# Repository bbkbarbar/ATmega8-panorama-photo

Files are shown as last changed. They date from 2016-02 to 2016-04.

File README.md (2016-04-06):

# Panorama-photo

## Project goal:
Create a device what can rotate camera (or camera-mounted phone) around Z axis to create perfect panorama photos or time-lapse videos.

### Functionality:
With this device the **user can create panorama photos** without "fitting problems"  
**or** can create **time-lapse videos with** using (very) slowly **rotating camera**.  
This device can be placed between any standard camera-tripod (or any other camera-mount) and the camera (or any other device what can be placed on a standard tripod (will be called as "camera" below)).
It can rotate the camera to selected direction with selected speed.
The device works from standard lithium battery with built-in battery charger.

### Features:
 - User can select the direction of rotating
 - User can select the speed of rotating
 - Device can be mounted in any standard tripod (or any other device what uses standard mount-screw)
 - Any camera, cellphone mount or any other devices can be mounted on the top of this device which can be mounted on a standard tripod
 - User can set the position of mounted device in 2 axis to reach the optimal position of camera (where the camera's lens is exactly above the center point of rotation)
 - Works with using a replaceable Li-ion battery (in size of 18650)
 - Contains built-in battery charger module (charging current max 1A from micro-usb port)
 - User can interrupt the process during rotation. (since v1.2) 

### MCU: 
**Required features:**
 - PWM output (~50Hz) (1)
 - Analog input (at least 2 channel)
 - I/O input (at least 2)
 - I/O output (at least 2)
 - Low energy consumption
 
**Selected device** (MCU): Atmel **AVR ATmega8** ([DataSheet](https://github.com/bbkbarbar/ATmega8-panorama-photo/blob/master/Docs/ATmega8_datasheet.pdf))

#### Sequence diagram of states (v1.2)
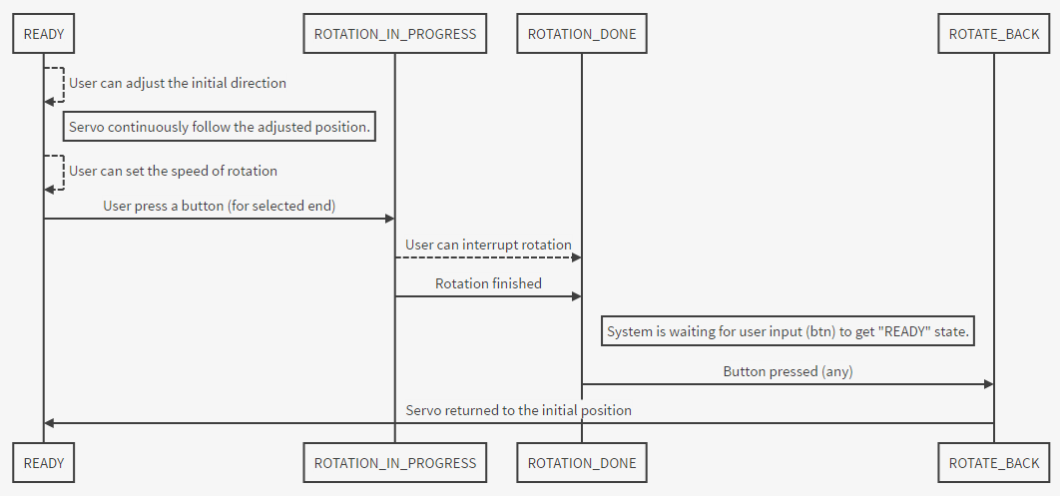
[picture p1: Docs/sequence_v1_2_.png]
Basic sequence diagram


#### First "mainly working" version on testboard:

<a href="http://www.youtube.com/watch?i8isvKmdPvMfeature=player_embedded&v=33iNxKAsr9w
" target="_blank">IMAGE ALT TEXT HERE</a>

#### First test device (mechanism and box built from Lego):
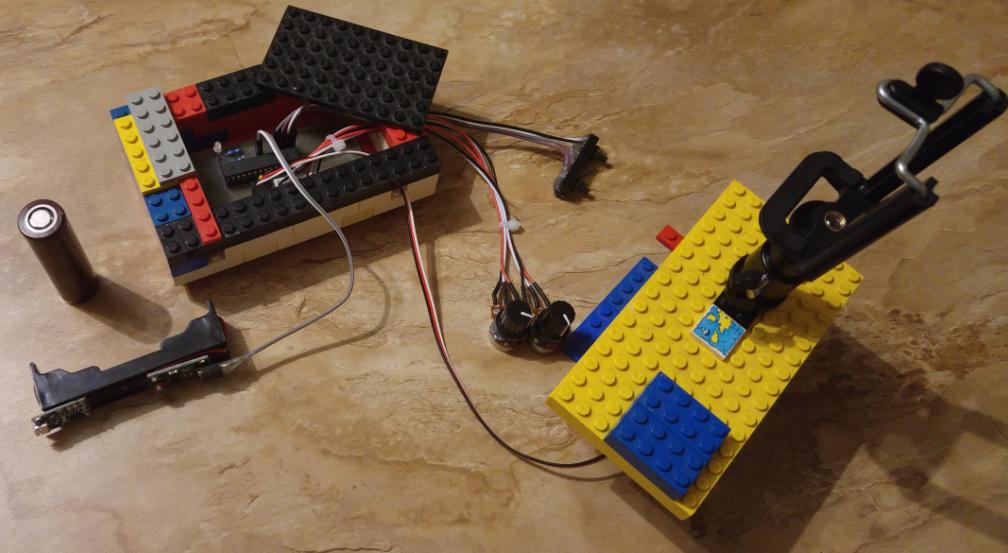
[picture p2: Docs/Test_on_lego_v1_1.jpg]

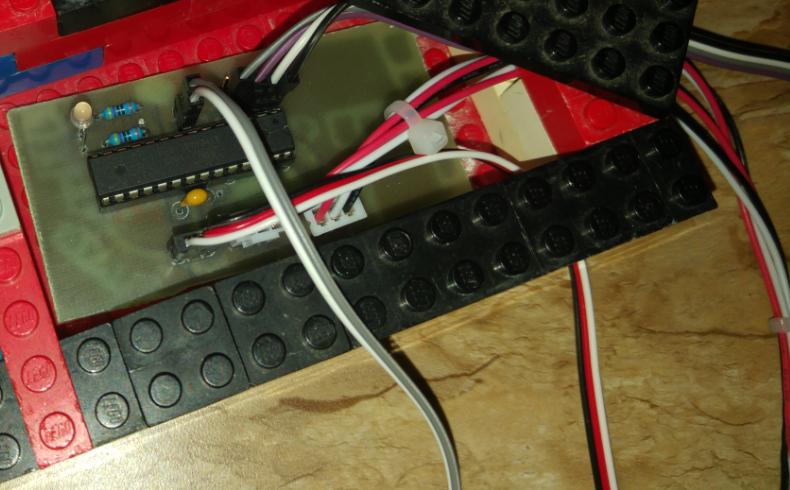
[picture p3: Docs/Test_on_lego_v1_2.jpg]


**[Photo album](https://goo.gl/photos/7FJK6yykkkFa5fTw9)**

**UseCase diagram**

[First version can be seen here..](https://github.com/bbkbarbar/ATmega8-panorama-photo/blob/master/Docs/useCase_plan_1.png)

[Previous test #1](https://youtu.be/i8isvKmdPvM)

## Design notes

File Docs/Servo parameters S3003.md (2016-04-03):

# Servo type: Futaba S3003
https://www.servocity.com/html/s3003_servo_standard.html#.VwD2R5yLSt9

Control System:                 +Pulse Width Control 1520usec Neutral
Required Pulse:                 3-5 Volt Peak to Peak Square Wave
Operating Voltage:              4.8-6.0 Volts
Operating Temperature Range: 	-20 to +60 Degree C
Operating Speed (4.8V):         0.23sec/60 degrees at no load
Operating Speed (6.0V):         0.19sec/60 degrees at no load
Stall Torque (4.8V):            44 oz/in. (3.2kg.cm)
Stall Torque (6.0V):            56.8 oz/in. (4.1kg.cm)
Operating Angle:                45 Deg. one side pulse traveling 400usec
Continuous Rotation Modifiable: Yes
Direction:                      Counter Clockwise/Pulse Traveling 1520-1900usec
Current Drain (4.8V):           7.2mA/idle
Current Drain (6.0V):           8mA/idle
Motor Type:                     3 Pole Ferrite
Potentiometer Drive:            Indirect Drive 
Bearing Type:                   Plastic Bearing
Gear Type:                      All Nylon Gears
Connector Wire Length:          12" (~305mm)
Dimensions:                     1.6" x 0.8"x 1.4" (41 x 20 x 36mm)
Weight:                         1.3oz. (37.2g)

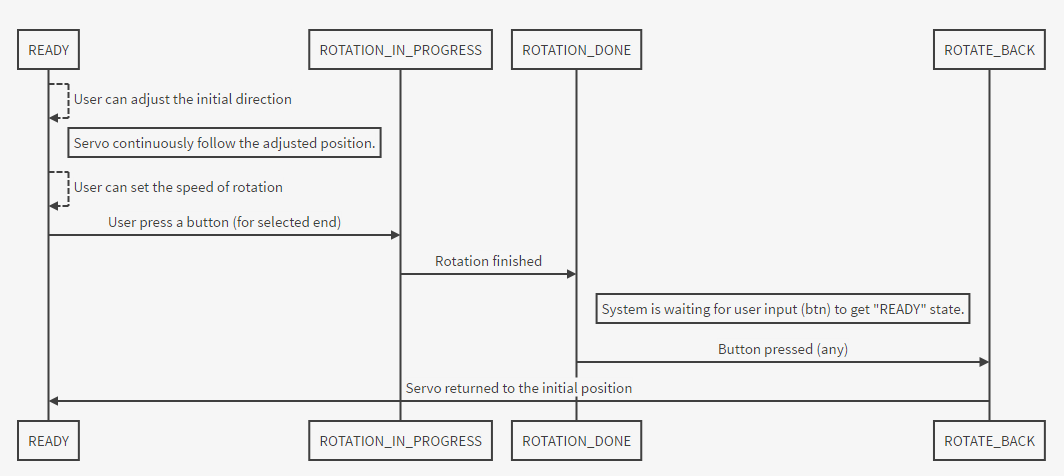
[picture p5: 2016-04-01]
Docs/sequence_v1_1_.png

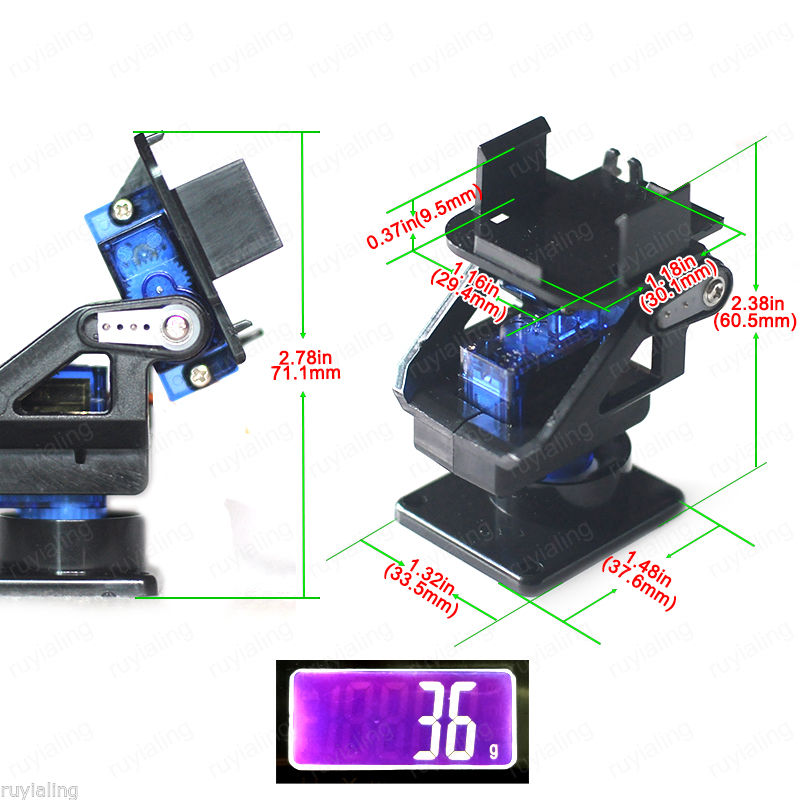
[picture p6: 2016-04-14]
Docs/Servo_hw/Servo_arm_for_phones.jpg

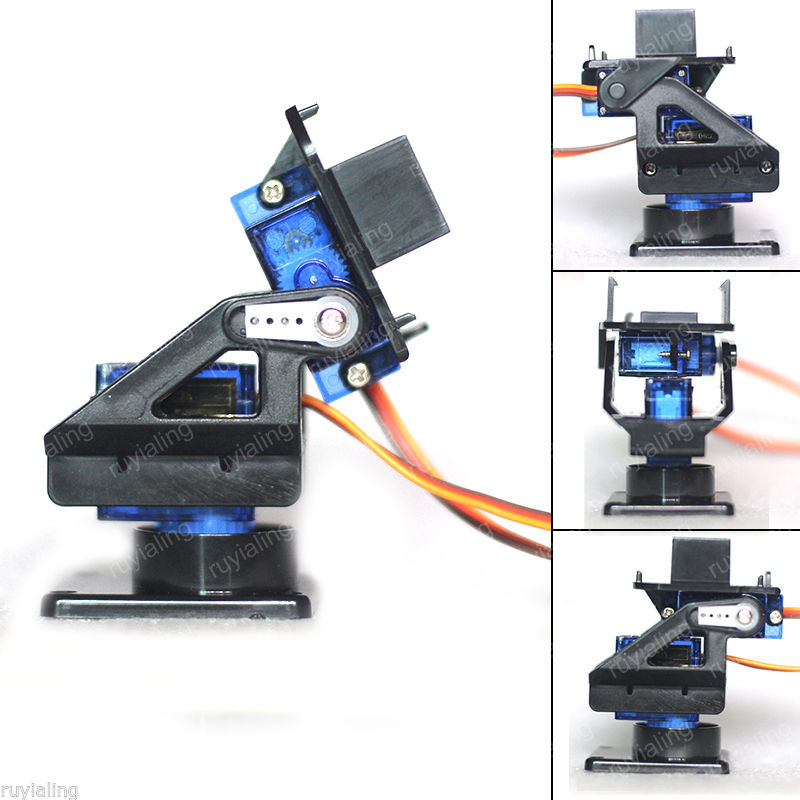
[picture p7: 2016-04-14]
Docs/Servo_hw/Servo_arm_for_phones (1).jpg

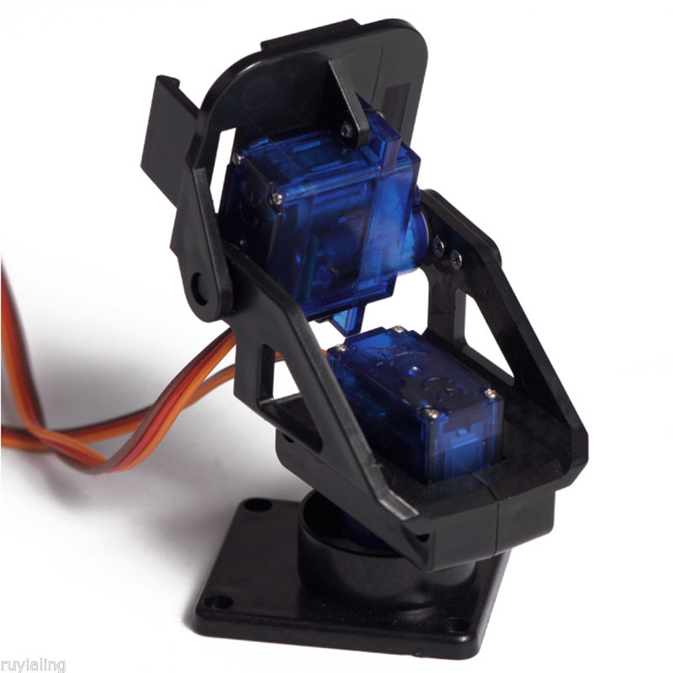
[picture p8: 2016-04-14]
Docs/Servo_hw/Servo_arm_for_phones (2).jpg

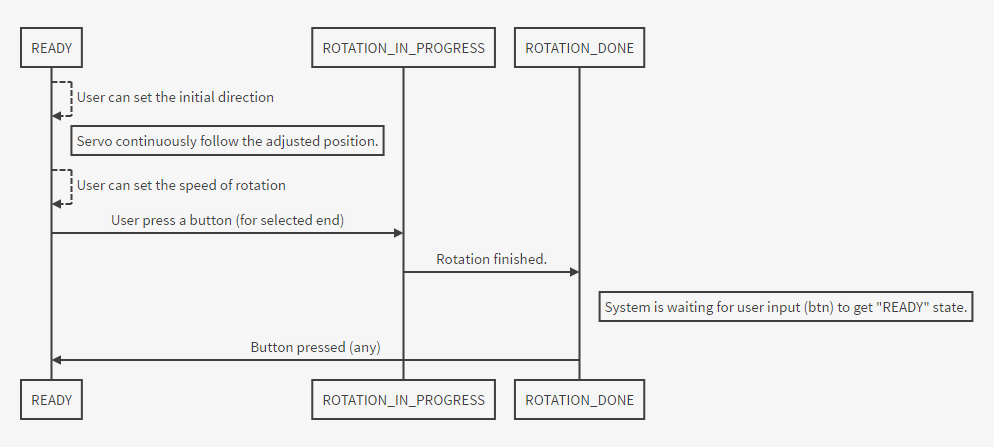
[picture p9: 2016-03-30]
Docs/Sequence.png

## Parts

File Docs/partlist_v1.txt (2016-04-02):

Partlist

Exported from ATmega8_panorama-photo_v2.sch at 2016.04.02. 10:25:53

EAGLE Version 5.10.0 Copyright (c) 1988-2010 CadSoft

Part            	Device							Package  	Library  		

ATMEGA8             DIL28-3      					DIL28-3    	ic-package
C1                  Ceramic capacitator     		C2.5-3     	capacitor-wima
LED_RG              connector - 3 pin				MA03-1     	con-lstb
POT1                connector - 3 pin				MA03-1     	con-lstb
POT2            	connector - 3 pin				MA03-1     	con-lstb
PWR_SUPPLY_CONN     connector - 2 pin				22-23-2021 	con-molex
R1                  R-EU_0204/7  					0204/7     	resistor
R2                  R-EU_0204/7  					0204/7     	resistor
R5                  R-EU_0207/5V 					0207/5V    	resistor
R6                  R-EU_0207/5V 					0207/5V    	resistor
SERVO               connector - 3 pin				MA03-1     	con-lstb
SV1                 connector - 2x3 pin or 1x4 pin	MA03-2     	con-lstb

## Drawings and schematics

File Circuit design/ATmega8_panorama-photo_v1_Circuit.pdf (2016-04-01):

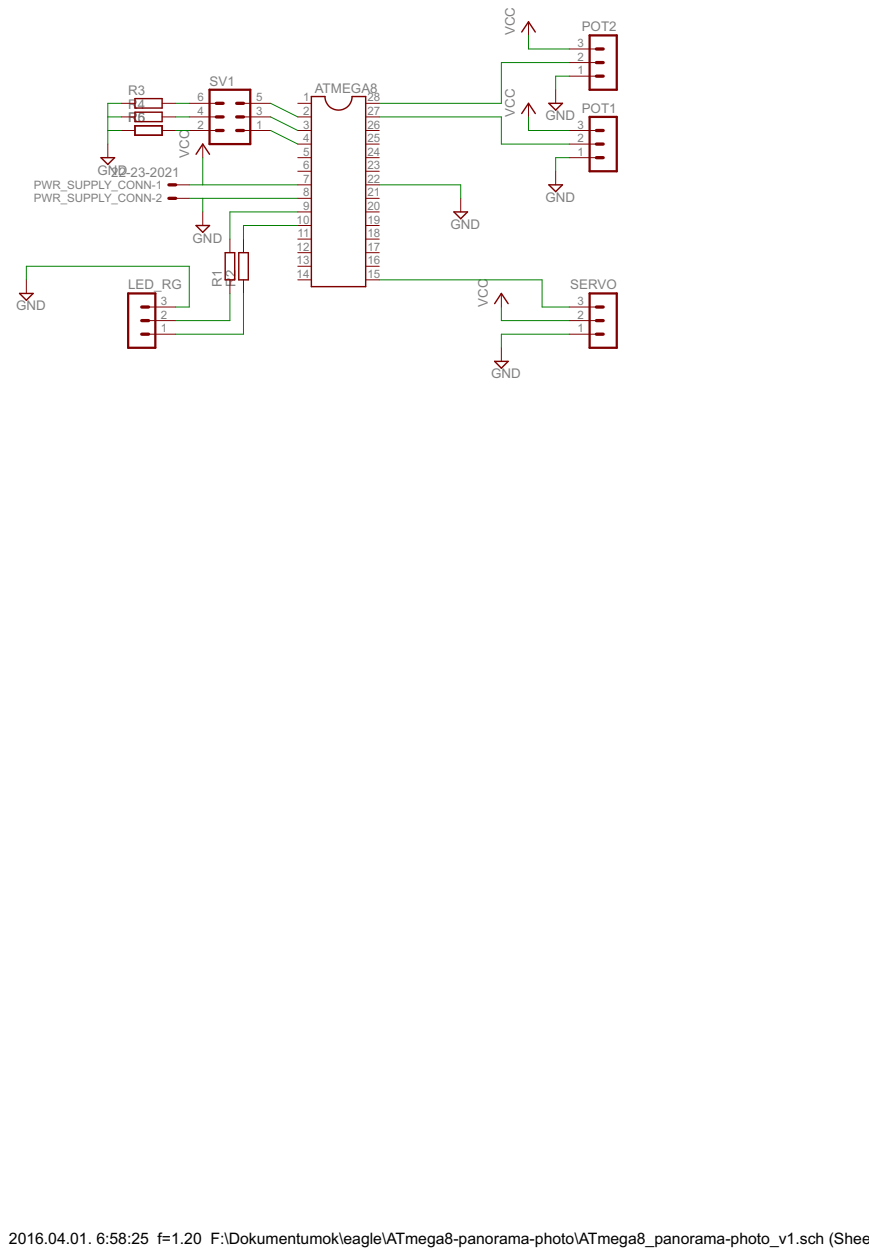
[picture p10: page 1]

2016.04.01. 6:58:25 f=1.20 F:\Dokumentumok\eagle\ATmega8-panorama-photo\ATmega8_panorama-photo_v1.sch (Sheet: 1/1)

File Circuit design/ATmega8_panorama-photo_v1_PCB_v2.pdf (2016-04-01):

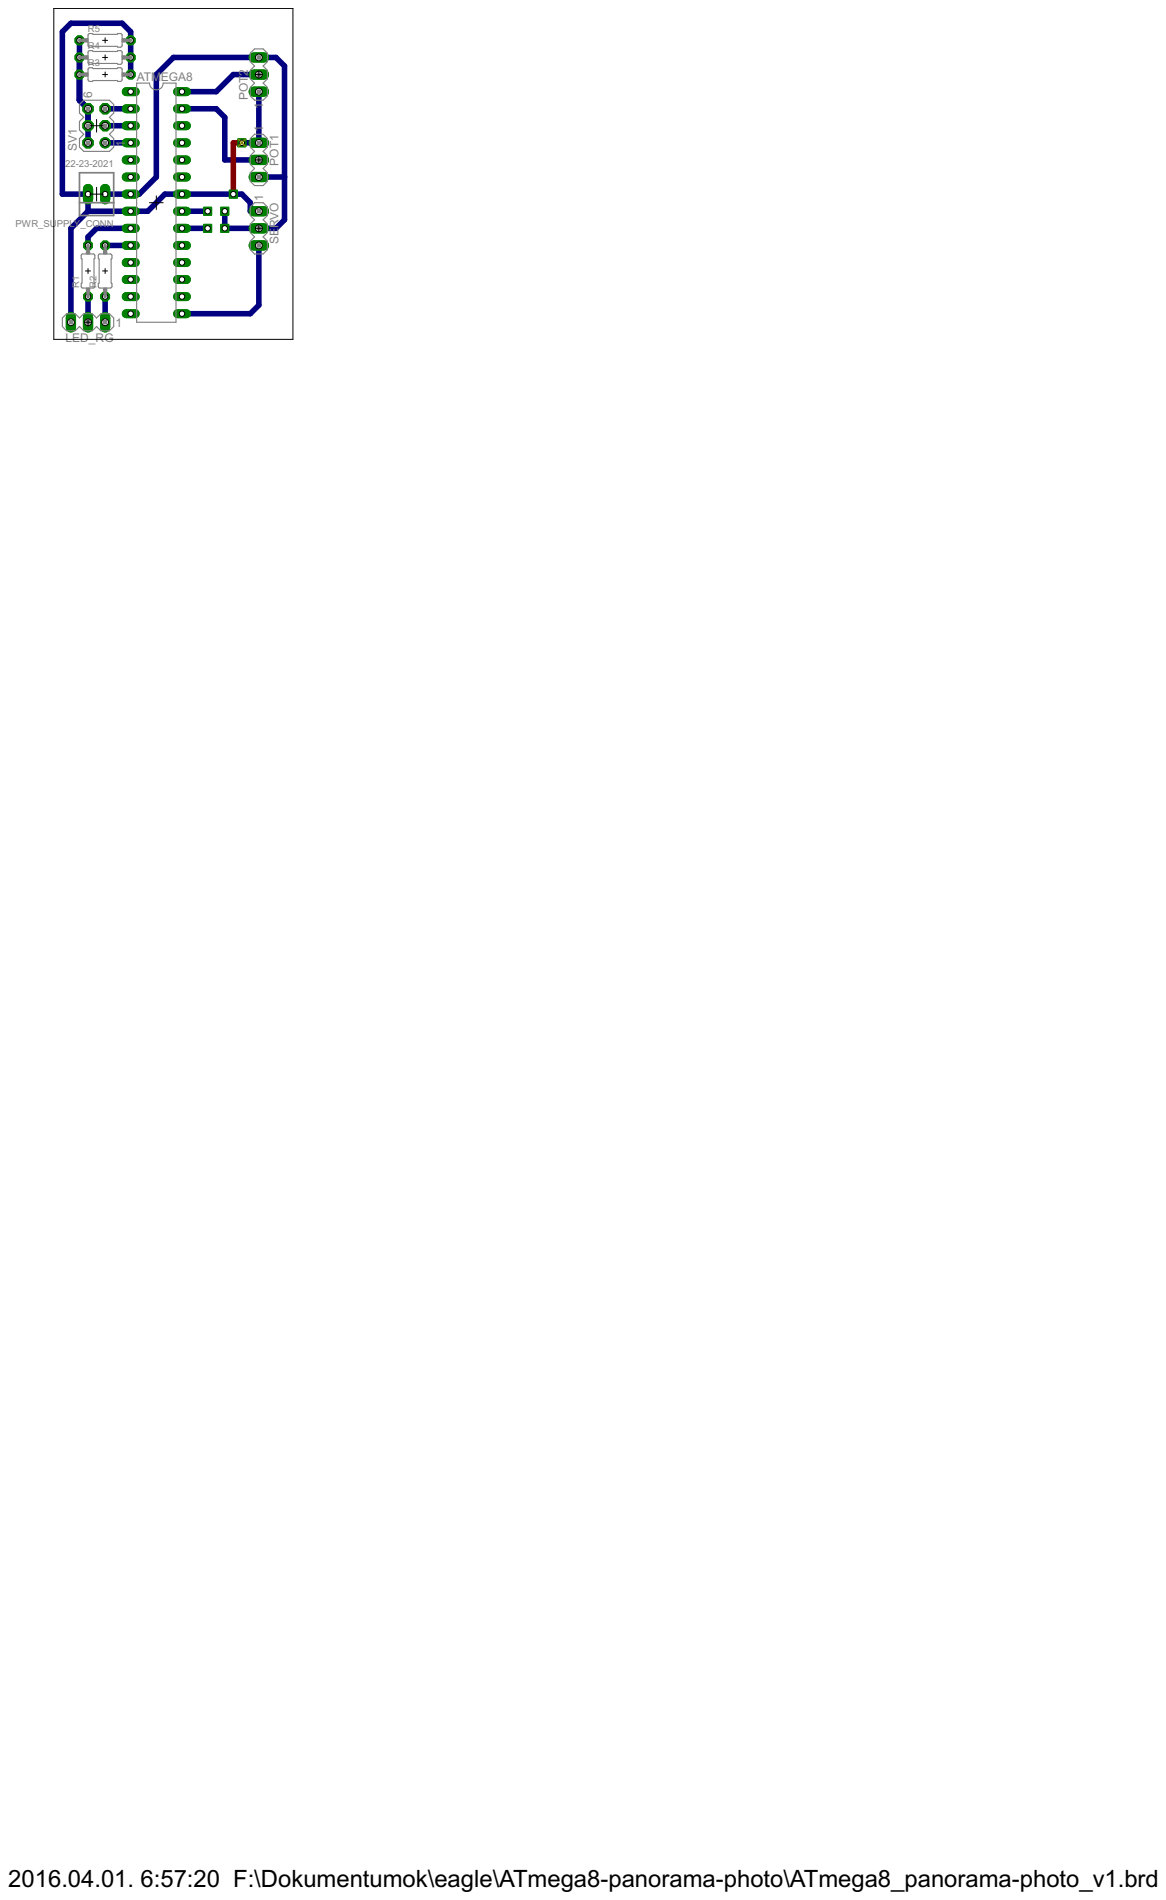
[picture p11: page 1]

2016.04.01. 6:57:20 F:\Dokumentumok\eagle\ATmega8-panorama-photo\ATmega8_panorama-photo_v1.brd

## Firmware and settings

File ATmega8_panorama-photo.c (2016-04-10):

 /*************************************\
 *        Panorama-photo v1.2          *
 *                                     *
 *  Device: ATmega8                    *
 *          mega8L-8PU - OK            *
 *          mega8-16PU - ??            *
 *  Deploy configuration:              *
 *   SUT_CKSEL: ________               *
 *   ISP freq: 115.2 kHz               *
 *                                     *
 *                                     *
 *  Pin configuration:                 *
 *   @used:                            *
 *   - Button 1:   PD0                 *
 *   - Button 2:   PD1                 *
 *   - Potmeter 1: PC5 (ch5)           *
 *   - Potmeter 2: PC4 (ch4)           *
 *   - Servo:      PB1 (OC1A)          *
 *   - LED1-green: PB7                 *
 *   - LED1-red:   PB6                 *
 *                                     *
 *  Pin configuration @TEST:           *
 *   - Button 1:   PB5                 *
 *   - Button 2:   PB4                 *
 *   - LEDBAR:     PD0-7               *
 *                                     *
 *  Test: WORKS on target board v1.0   *
 *                                     *
 *         Boor Andras  @ 2016         *
 *                                     *
 \*************************************/

//#define TEST
//#define SPIKE
#define TESTBOARD
//#define ENABLE_ROTATE_BACK

#define F_CPU 1000000

#include "lib/ATmega8_read_ADC.c"
#include "lib/ATmega8_servo_control.c"
#ifdef TESTBOARD
#include "lib/bar_display.c"
#endif


#ifndef DELAY_INCLUDED
    #include <util/delay.h>
    #define DELAY_INCLUDED
#endif


/////////////////////////////////////     HW DEFINITIONS    /////////////////////////////////////
// LED
#define PORT_OF_LEDS                PORTB
#define LED_PIN_GREEN               7
#define LED_PIN_RED                 6

// BUTTON
#ifndef TESTBOARD
    #define PORT_INPUT_OF_BUTTONS   PIND
    #define PORT_OF_BUTTONS         PORTD
    #define BUTTON_1_PIN            0
    #define BUTTON_2_PIN            1
#else
    #define PORT_INPUT_OF_BUTTONS   PINB
    #define PORT_OF_BUTTONS         PORTB
    #define BUTTON_1_PIN            5
    #define BUTTON_2_PIN            4
#endif
//#define BUTTON_3_PIN              2                                         // inactive in v1

#define BTN_1                       (PORT_INPUT_OF_BUTTONS >> BUTTON_1_PIN)
#define BTN_2                       (PORT_INPUT_OF_BUTTONS >> BUTTON_2_PIN)
//#define PIN_BTN_3                 (PORT_INPUT_OF_BUTTONS >> BUTTON_3_PIN)   // inactive in v1
#define BTN_RIGHT                   BTN_1
#define BTN_LEFT                    BTN_2

// Read button states
#define isPressed(x)                ((x & 0b1) == 0)
#define isReleased(x)               ((x & 0b1) == 1)


// ADC channels of potmeters
#define POT_TEST                    0
#define POT1                        5
#define POT2                        4

// States of feedback LED
#define OFF                         0
#define GREEN                       1
#define RED                         2
#define YELLOW                      3

#ifdef TESTBOARD
    #define LEDBAR                  PORTD
#endif

//////////////////////////////////////        OTHERS         ////////////////////////////////////
#define DEFAULT_DELAY               100

#define POT_MAX_VALUE               1023

#define RIGHT_END_POSITION          SERVO_RIGHT
#define LEFT_END_POSITION           SERVO_LEFT

// Identify direction (of previously pressed button)
#define NONE                        0
#define RIGHT                       1
#define LEFT                        2

#define INC_TO_RIGHT                (-1)
#define INC_TO_LEFT                 (1)


// System wait for BUTTON_RELEASE_DELAY ms before do the next command
// to avoid unwanted re-detection of buttonPress on same button.
#define BUTTON_RELEASE_DELAY        500

// Minimum delay in continous rotation to prevent from to fast rotating
#define MIN_DELAY_FOR_ROTATION      50

// TRY to prevent servo "quake" symptom
#define DELAY_AFTER_SERVO_ROTATION_IN_READY_STATUS 30

// For using tighten servo degree to prevent problems 
// coused by servo's internal limit-detection
#define SERVO_EDGE_THRESHOLD        100

// Used when system is in "ROTATE_BACK" state
// and need to determine when servo almost reached the adjusted initial position
#define SERVO_ROTATE_BACK_THRESHOLD 50

//////////////////////////////////////        STATES         ////////////////////////////////////
// Ready to use. User can set initial direction and speed.
// System is waiting for start input (btn). (Servo continuously follow the setted position.)
#define READY                       1
// Rotation started, but not finished yet.
#define ROTATION_IN_PROGRESS        2
// Rotation finished.System is waiting for user input (btn) to get "ROTATE_BACK" state.
#define ROTATION_DONE               3
// Servo rotating back before get "READY" state.
#define ROTATE_BACK                 4


// Additional information can be displayed on ledbar (in unused io-ports)
// when configuration runs in testboard.
#ifdef TESTBOARD
    void showValueOnLedBar(unsigned short value, unsigned short min, unsigned short max){
        LEDBAR = getValueToShow(
            value - min, 
            max - min
        );
    }
#endif


// Wait function can be used instead of direct usage of "_delay_ms(val)" function
// because of the input range problem of "_dalay_ms()" function.
void wait(unsigned short val) {
    while(val--) _delay_ms(1);
}

void _wait(){
    _delay_ms(DEFAULT_DELAY);
}


// Set color of feedback led (RG)
void setLed(unsigned short color){
    if(color == GREEN){
        PORT_OF_LEDS &= ~(1 << LED_PIN_RED); 
        PORT_OF_LEDS |=  (1 << LED_PIN_GREEN);
    }else
    if(color == RED){
        PORT_OF_LEDS |=  (1 << LED_PIN_RED); 
        PORT_OF_LEDS &= ~(1 << LED_PIN_GREEN);
    }else
    if(color == YELLOW){
        PORT_OF_LEDS |=  (1 << LED_PIN_RED); 
        PORT_OF_LEDS |=  (1 << LED_PIN_GREEN);
    }else{
        PORT_OF_LEDS &= ~(1 << LED_PIN_RED); 
        PORT_OF_LEDS &= ~(1 << LED_PIN_GREEN);
    }
}


// Determine conditions when servo reached any end position
#define isRotationDone() ( ((btnPressedPreviously == RIGHT && (getServoPosition() > RIGHT_END_POSITION + SERVO_EDGE_THRESHOLD)) || (btnPressedPreviously == LEFT && (getServoPosition() < LEFT_END_POSITION - SERVO_EDGE_THRESHOLD)))?0:1 )


// Calculate difference between given values (can not be negative)
unsigned short diff(unsigned short x, unsigned short y){
    return ( ((x)>(y))?((x)-(y)):((y)-(x)) );
}


// Modify servo direction with given value
void rotateServo(short value){
    setServoPosition( getServoPosition() + value );
}


// Calculate delay between iteration steps of rotation
unsigned short calculateDelayOfRotationSteps(uint16_t speedInput){
    return (unsigned short)( MIN_DELAY_FOR_ROTATION + speedInput );
}


// Calculate servoPosition from potmeter input
unsigned short calculateServoPositionFromDirectionInput(uint16_t positionInput){
    return ( ((unsigned short) (POT_MAX_VALUE - positionInput) * 1.9f) + SERVO_OUTPUT_MIN );
}


void init(){   
    //                 LED
    // Set LED pins as output
    DDRB |= (1 << LED_PIN_GREEN) 
         |  (1 << LED_PIN_RED);

    //              POTMETERS
    // DDRC set as input for ADC in initADC() function

    //                SERVO
    // Output of servo set as output initServoControl() function
          
    //DDRB = (1<<PB0)|(1<<PB4)|(1<<PB5)|(1<<PB6)|(1<<PB7);

    //               BUTTONS
    // Setup the pull-up resistor for buttons 
    PORT_OF_BUTTONS |= (1 << BUTTON_1_PIN) 
                    |  (1 << BUTTON_2_PIN);
    //PORTB |= 0b10000000; //PB7 pin for TEST

    #ifdef TESTBOARD
        DDRD = 0xFF;
        LEDBAR = 170;
    #endif
}


int main(){

    init();
    initADC();
    initServoControl();

#ifndef SPIKE
    
    uint16_t positionInput = 0, speedInput = 0;
    #ifdef TESTBOARD
    #ifdef TEST
        unsigned short m, n;
    #endif
    #endif


    // Initialize values and feedback according to get READY state..
    unsigned char btnPressedPreviously = NONE;
    unsigned char currentState = READY;
    setLed(GREEN);

    while(1){
        
        if(currentState == READY){ 
            
            // User can set initial direction and speed.
            speedInput =    readADC(POT2);
            if(speedInput > 800){
                speedInput *= 2;
            }
            #ifdef TESTBOARD
                showValueOnLedBar( (unsigned short)speedInput, 0, POT_MAX_VALUE*2);
            #endif
            
            positionInput = readADC(POT1);

            // Show "value-quaking" of positionInput
            #ifdef TESTBOARD
                #ifdef TEST
                    m = ((unsigned short)(positionInput / 10) * 10); // round to
                    n = m + 8;
                    showValueOnLedBar( (unsigned short)positionInput, m, n );
                #endif
            #endif

            // Servo continuously follow the setted position.
            setServoPosition( calculateServoPositionFromDirectionInput(positionInput) );

            // Prevent servo "quake" symptom (seems partly helps)
            //wait(DELAY_AFTER_SERVO_ROTATION_IN_READY_STATUS); // @If PASSED remove after next test

            // System is waiting for start input (btn). 
            if( btnPressedPreviously == NONE ){

                if(isPressed(BTN_RIGHT)){
                    btnPressedPreviously = RIGHT;
                }else
                if(isPressed(BTN_LEFT)){
                    btnPressedPreviously = LEFT;
                }
                
            }else{ //if any button is pressed previously then need to wait until button is released.

                if( ((btnPressedPreviously == RIGHT) && (isReleased(BTN_RIGHT))) ||
                    ((btnPressedPreviously == LEFT ) && (isReleased(BTN_LEFT ))) ){ 
                    // button what has been pressed previously AND released now..
                    // btnPressedPreviously variable stores the identifier of button what has been released just now.

                    // Set values and feedback according to get ROTATION_IN_PROGRESS state
                    setLed(RED);
                    currentState = ROTATION_IN_PROGRESS;
                    wait(BUTTON_RELEASE_DELAY);

                }

            }

        } // eof READY state

        else

        if(currentState == ROTATION_IN_PROGRESS){ // Rotation started, but not finished yet.

            // Option for user to interrupt rotation progress
            if( (isPressed(BTN_LEFT)) && (isPressed(BTN_RIGHT)) ){
                setLed(OFF);

                // wait until all button released
                while( (isPressed(BTN_LEFT)) || (isPressed(BTN_RIGHT)) ){
                    wait(BUTTON_RELEASE_DELAY);
                }

                // When all button released get ROTATION_DONE state
                currentState = ROTATION_DONE;
                btnPressedPreviously = NONE;
                setLed(YELLOW);
            }

            else

            if(isRotationDone()){

                // Set values and feedback according to get ROTATION_DONE state
                btnPressedPreviously = NONE;
                currentState = ROTATION_DONE;
                setLed(YELLOW);

            }else{

                if(btnPressedPreviously == RIGHT){
                    
                    #ifdef TESTBOARD
                        showValueOnLedBar( getServoPosition(), SERVO_OUTPUT_MIN, SERVO_OUTPUT_MAX );
                    #endif
                    
                    rotateServo(INC_TO_RIGHT);
                    wait( calculateDelayOfRotationSteps(speedInput) );

                }
                else

                if(btnPressedPreviously == LEFT){
                    
                    #ifdef TESTBOARD
                        showValueOnLedBar( getServoPosition(), SERVO_OUTPUT_MIN, SERVO_OUTPUT_MAX );
                    #endif
                    
                    rotateServo(INC_TO_LEFT);
                    wait( calculateDelayOfRotationSteps(speedInput) );

                }

            }

        } // eof ROTATION_IN_PROGRESS

        else

        if(currentState == ROTATION_DONE){ // Rotation finished. 

            // System is waiting for user input (button press and release) 
            // before servo returns to initial direction and get "READY" state. 

            // Check that any button is pressed..
            if(btnPressedPreviously == NONE){

                if(isPressed(BTN_RIGHT)){
                    btnPressedPreviously = RIGHT;
                }else
                if(isPressed(BTN_LEFT)){
                    btnPressedPreviously = LEFT;
                }

            }else{

                // Check that previously pressed button is released..
                if( ((btnPressedPreviously == RIGHT) && (isReleased(BTN_RIGHT))) ||
                    ((btnPressedPreviously == LEFT ) && (isReleased(BTN_LEFT ))) ){
                    
                    #ifdef ENABLE_ROTATE_BACK                    
                        // re-read position input before get ROTATE_BACK state..
                        positionInput = readADC(POT1);

                        // Set values and feedback according to get ROTATE_BACK state
                        currentState = ROTATE_BACK;
                        setLed(OFF);
                        btnPressedPreviously = NONE;
                    #endif

                    #ifndef ENABLE_ROTATE_BACK
                        // Set values and feedback according to get ROTATE_BACK state
                        currentState = READY;
                        btnPressedPreviously = NONE;
                        setLed(GREEN);
                    #endif

                    wait(BUTTON_RELEASE_DELAY);

                }

            }

        } // eof ROTATION_DONE

        else

        if(currentState == ROTATE_BACK){

            unsigned short wantedPosition = calculateServoPositionFromDirectionInput(positionInput);
            uint8_t direction;

            // Note: RIGHT < LEFT
                    //2400               1500
            if( getServoPosition() > wantedPosition ){ // need to rotate right (--)
                direction = INC_TO_RIGHT;
            }else{ // need to rotate left (++)
                direction = INC_TO_LEFT;
            }

            short attempsToRotateBack = 0;

            //               900
            unsigned short distance;
            //            900 .. 890 .. 880 ..                            >  50
            while( ((distance = diff(getServoPosition(), wantedPosition))  > SERVO_ROTATE_BACK_THRESHOLD) && (attempsToRotateBack < 300) && (attempsToRotateBack >= 0) ){ // Need to rotate back..

                if(attempsToRotateBack < 10){ // to fine starts
                    rotateServo( direction );
                }else

                if( distance > 400 ){
                    rotateServo( direction * 10 );
                }else
                if( distance > 250 ){
                    rotateServo( direction * 5 );
                }else
                if( distance > 150 ){
                    rotateServo( direction * 2 );
                }else{
                    rotateServo( direction );
                }

                attempsToRotateBack++;

                wait(20);

            }

            // Set values and feedback according to get READY state 
            currentState = READY;
            btnPressedPreviously = NONE;
            setLed(GREEN);

        } // eof ROTATE_BACK

    }

#endif
#ifdef SPIKE

    setLed(YELLOW);
    while(1){

        // TestCode here
        positionInput = readADC(POT1);
        speedInput =    readADC(POT2);

        #ifdef TESTBOARD
            unsigned char output = 0;
            output |= getValueToShow(positionInput / 2, POT_MAX_VALUE/2);
            output |= getValueToShow(speedInput / 2, POT_MAX_VALUE/2) << 4;
            LEDBAR = output;
        #endif

    }

#endif

    return 0;

}

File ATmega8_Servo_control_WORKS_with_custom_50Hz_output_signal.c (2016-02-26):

#define F_CPU 1000000

#include <avr/io.h>
#include <util/delay.h>

#define SEC_IN_US	  1000000

//////////////////////////////// 	PORT DEFINITIONS	////////////////////////////////
#define OUTPUT_PORT		PORTD
#define SERVO_PORT		PORTD


//////////////////////////////// 	PIN  DEFINITIONS	////////////////////////////////
#define SERVO_PIN		  PD0
#define FEEDBACK_PIN1	  PD3
#define FEEDBACK_PIN2	  PD4

#define SIGN_COUNT		  50

//////////////////////////////// 		OTHERS			////////////////////////////////
#define	DEFAULT_DELAY 			 100
#define SERVO_PWM_WIDTH_IN_US 	2000


void wait(unsigned short val) {

    while(val--) _delay_ms(1);

}

void _wait(){
	_delay_ms(DEFAULT_DELAY);
}

void wait_us(double val){
	while(val--) _delay_us(1);
}


/*
 *	"ProgressBar" on portD
 */
void showByteValueOnBar(unsigned int val){
	
	if(val > 16){
		PORTD =         0b1;
	}
	if(val > 48){
		PORTD |=       0b10;	
	}
	if(val > 80){
		PORTD |=      0b100;
	}
	if(val > 112){
		PORTD |=     0b1000;
	}
	if(val > 144){
		PORTD |=    0b10000;
	}
	if(val > 176){
		PORTD |=   0b100000;
	}
	if(val > 208){
		PORTD |=  0b1000000;
	}
	if(val > 240){
		PORTD |= 0b10000000;
	}

}


void init(){   // 76543210
		DDRB  = 0b11111111;
	  	DDRC  =  0b0000000;
  	  	DDRD  = 0b11111111;
	  	
		PORTC = 0;
	  	PORTD = 0x01;
	  	
	  //DDRB = (1<<PB0)|(1<<PB4)|(1<<PB5)|(1<<PB6)|(1<<PB7);
}


/*==========================================================================*
 *			 	ADC (10bit) (tested in channel 0 and channel 5)			   	*
 *							 Tested on ATmega8			   					*
 *		  DDRC seems doesn't matter (it works when DDRC = 0b11101111)		*
 *							 Boor Andras - 2014			   					*
 *==========================================================================*/
void initADC() {
    //         76543210
    ADMUX  = 0b01000000;
    ADCSRA = 0b10000111;
} 


uint16_t readADC(uint8_t ch) {

    ADMUX = (ADMUX & 0b11110000) | ch;
//  01000001    ADMUX jelenlegi állapota (1-es ADC csatorna beállítva)
//& 11110000    ezzel toroljuk az elozo portok kivalasztast
//= 01000000    eredmenynek kapjuk az eredeti ADMUX beallitast
//| 00000101    "rairjuk" az ADC csatornat
//= 01000101    
    ADCSRA|=(1<<ADSC);          // konverzió elindítás
    while(ADCSRA & (1<<ADSC));  // várás az átalakításra

    return (ADCL | (ADCH<<8));  // adc érték visszaadása
}


double calculateServoVal(int degree){
	// 	-90° => 1.0 ms
	// 	  0° => 1.5 ms
	//  +90° => 2.0 ms

	double usVal = (((degree + 90)/90) * 500) + 1000;
	return usVal;

}


void setServoDegree(int degree){
	double servoVal = calculateServoVal(degree);
	int i;
	for(i=0; i<2000; i++){
		
		SERVO_PORT |= (1<<SERVO_PIN);
        wait_us(servoVal);
    	
        SERVO_PORT &= ~(1<<SERVO_PIN);	
		double freeTime = SERVO_PWM_WIDTH_IN_US - servoVal;
        wait_us(freeTime); 

	}	
}


void feedback(unsigned char state){
	
	//RM if(state == 1 || state == 3){
	if(state & 0b01){
		OUTPUT_PORT |=  (1<<FEEDBACK_PIN1);
	}else{
		OUTPUT_PORT &= ~(1<<FEEDBACK_PIN1);
	}

	//RM if(state == 2 || state == 3){
	if(state & 0b10){
		OUTPUT_PORT |=  (1<<FEEDBACK_PIN2);
	}else{
		OUTPUT_PORT &= ~(1<<FEEDBACK_PIN2);
	}

}


void generateOutputForFrequencyMeasurement(double freqencyInHz, float pct){
	
	float fillFactor = pct / 100;
	if(fillFactor > 1){
		fillFactor = 1;
	}
	if(fillFactor < 0){
		fillFactor = 0;
	}
	double tCycle = (1 / freqencyInHz) * SEC_IN_US;
	double tOnInUs  = tCycle * fillFactor;
  	double tOffInUs = tCycle * (1-fillFactor);
	//double tOffInUs = tOnInUs;
  	//double tOffInUs = (tCycle - tOnInUs);

	int i;
	for(i = 0; i < SIGN_COUNT; i++){

		SERVO_PORT |=  (1<<SERVO_PIN);
		_delay_us(tOnInUs);

		SERVO_PORT &= ~(1<<SERVO_PIN);
		_delay_us(tOffInUs);

	}

}


int main(){

	init();
	//initADC();

	int degree = 0;
	unsigned char adc;

	float j;

	while(1){
		
		
		feedback(1);
		
		for(j = 0.5; j<7; j+= 0.25){  // 7*
			generateOutputForFrequencyMeasurement(6, j);			// j -> 2
		}		
		
		feedback(2);
		_delay_ms(2000);

		/*
		
		for(j = 1; j<0.5; j-= 1){
			generateOutputForFrequencyMeasurement(6, j);
		}
		
		_delay_ms(2000);
		*/

		/*
		adc = readADC(0);
		adc = (adc / 4);

		showByteValueOnBar(adc);		
		
		setServoDegree(adc);
		/**/


		/*
		degree = -89;
		setServoDegree(degree);

		degree = 0;
		setServoDegree(degree);

		degree = 89;
		setServoDegree(degree);
		/**/
	}

	return 0;

}

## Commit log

2016-02-26 remove current annotation
2016-02-26 remove *current.c -file
2016-03-16 Servo control and ADC works (in channel 5)
2016-03-16 Servo controled by ADC input (in steps)
2016-03-16 Servo continously controled by ADC input.
2016-03-26 Servo control functions moved to separated C file.
2016-03-26 Servo control functions used from separated C file.
2016-03-26 Add ADC functions as a separated C file
2016-03-28 Servo test with button and potmeter
2016-03-28 Basic circuit design created
    [ATmega8_panorama-photo_v1.sch]
2016-03-28 Circuit design done
    [ATmega8_panorama-photo_v1.sch]
2016-03-28 PCM design created for v1 of circuit
    [ATmega8_panorama-photo_v1.brd]
2016-03-30 Control flow inplemented, with more TODO-s
2016-03-30 Circuit design and PCB added as PDF
2016-03-30 Function of ROTATION_DONE -state implemented
    Some other modification added:
    - feedback on RG led added.
    - waiting after button released to avoid unwanted re-detection as a new buttonPress
    - etc
    [ATmega8_panorama-photo.c]
2016-03-30 TESTBOARD and TEST macros defined. LED output depend on conditional macros
2016-03-30 2 potmeter tested with ledBar
2016-03-30 2 potmeter tested with ledBar in same time
2016-03-31 Servo quake problems seems solved (at least much better now)
    [ATmega8_panorama-photo_with_servo_shaking_problem.c, ATmega8_panorama-photo_with_servo_shaking_problem_SOLVED.c]
2016-04-01 Quaking of positionInput shown in ledBar
2016-04-01 PCB faults corrected. AREF and AVCC pin ready to connect on PCB.
2016-04-01 Servo quaking problem SOLVED by connect AREF (and AVCC) pins to VCC.
    [ATmega8_panorama-photo.c]
2016-04-02 Schema and PCB v2 created
    [ATmega8_panorama-photo_v2.brd, ATmega8_panorama-photo_v2.sch]
2016-04-02 Working version on target board v1.0
2016-04-02 Upload images from LEGO test with PCB v1 #1
2016-04-03 Parameters of used servo added
2016-04-05 Interrupt function added (v1.2)
2016-04-05 Updated for version (v1.2)
    User interrupt during rotation added
2016-04-05 Interrupt function added
2016-04-05 Interrupt function added (v1.2)
    Interrupt function added for sequence diagram too..
    First verison of useCase diagram removed (replaced as link)
2016-04-14 Servo related documents added
